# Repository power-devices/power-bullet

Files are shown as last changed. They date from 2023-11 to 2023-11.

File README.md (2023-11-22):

# Welcome to the Power Bullet electronics repository

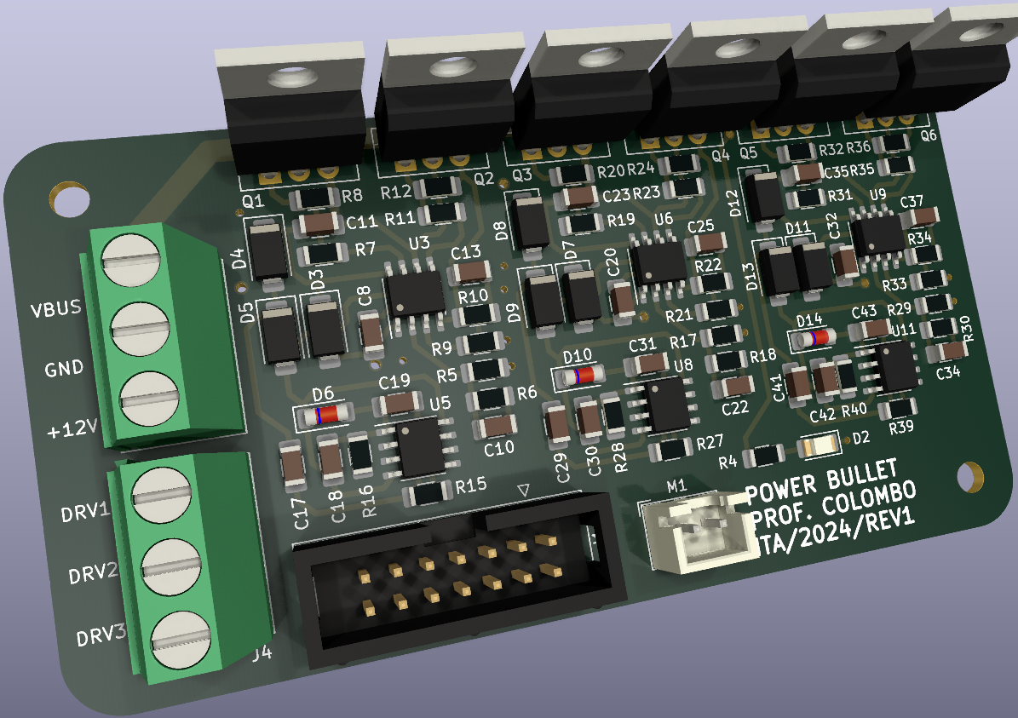
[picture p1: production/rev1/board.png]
REV1 board 3D model


I teach power electronics and I want to provide my students the best experience possible. This is the reason I created this project. I intend to allow people to produce power electronics devices at an extreme low cost. This board required 4 layers, but this is no problem today due to [JLCPCB](https://jlcpcb.com/) or other manufacturers.

So far, the project is divided into 3 pieces:

 1. Power supply: used to delivery power the other boards, it is compatible with mono-three phase up to 220 VAC
 2. Power bullet: a three phase h-bridge, simple as that
 3. Power brain F103: the main controller

# Disclaimer

I provide no warranty at all. Use it at your own risk!

# What will I find here?

You will find the design and production files. To edit the schematic/board you will need to install Kicad. I used version 7 to create this board.

# What can I do with this?

In this repository the board design and production files are stored. You are welcome to download/distribute it, use it, whatever.

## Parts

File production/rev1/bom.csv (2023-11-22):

Designator | Footprint | Quantity | Value | LCSC Part #
C1, C14, C20, C26, C32, C5, C8 | 1206 | 7 | 1uF
C10, C13, C22, C25, C34, C37 | 1206 | 6 | 33nF
C11, C23, C35 | 1206 | 3 | 1uF/50V
C15, C27 | 1206 | 2 | 1nF
C17, C29, C41 | 1206 | 3 | 10nF/50V
C18, C30, C42 | 1206 | 3 | 100nF/50V
C19, C31, C43 | 1206 | 3 | 1nF/50V
C2 | 1206 | 1 | 2n2
C4 | CP_EIA-3216-18_Kemet-A | 1 | 10uF
D10, D14, D6 | D_MiniMELF | 3 | ZMM15
D11, D3, D7 | D_SMA | 3 | 1N4007
D12, D13, D4, D5, D8, D9 | D_SMA | 6 | SS14
D2 | 1206 | 1 | LED
J1 | IDC-Header_2x07_P2.54mm_Vertical | 1 | Conn_02x07_Odd_Even
J3, J4 | TerminalBlock_Phoenix_MKDS-1,5-3_1x03_P5.00mm_Horizontal | 2 | Screw_Terminal_01x03
M1 | JST_XH_B2B-XH-A_1x02_P2.50mm_Vertical | 1 | Fan
Q1, Q2, Q3, Q4, Q5, Q6 | TO-220-3_Vertical | 6 | FDP11N50
R1 | 1206 | 1 | 120k
R10, R18, R22, R30, R34, R6 | 1206 | 6 | 3k3
R11, R17, R19, R21, R23, R29, R31, R33, R35, R5, R7, R9 | 1206 | 12 | 100R
R12, R20, R24, R32, R36, R8 | 1206 | 6 | 10k
R15, R16, R27, R28, R39, R40 | 1206 | 6 | 100k
R2 | 1206 | 1 | 1k5
R4 | 1206 | 1 | 220R
U11, U5, U8 | SOIC-8_3.9x4.9mm_P1.27mm | 3 | NE555D
U2 | SOT-223-3_TabPin2 | 1 | AMS1117-5.0
U3, U6, U9 | SOIC-8_3.9x4.9mm_P1.27mm | 3 | IR2101S
U4, U7 | SOIC-8_3.9x4.9mm_P1.27mm | 2 | ACS712xLCTR-05B

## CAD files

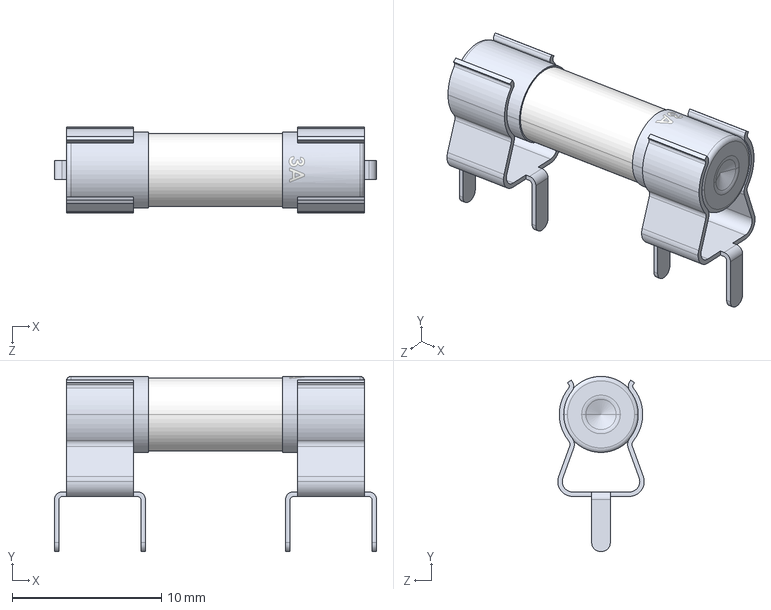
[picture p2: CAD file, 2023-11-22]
3d/Fuse Holder.STEP
21.6 x 11.8 x 5.80 mm
Fuse Clip x 2
3A Fuse

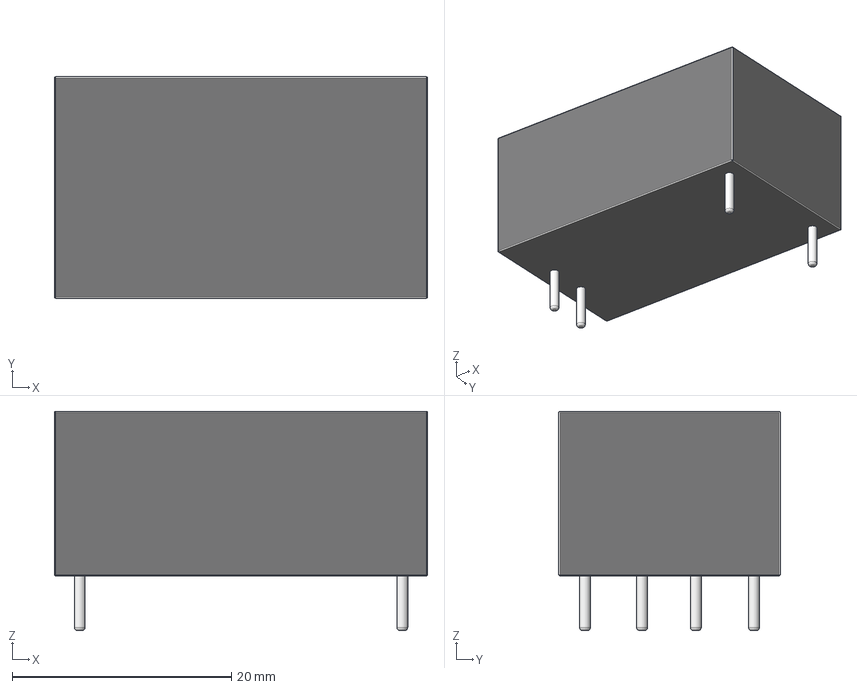
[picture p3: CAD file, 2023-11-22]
3d/hlk-pm01.step
34.0 x 20.2 x 20.0 mm

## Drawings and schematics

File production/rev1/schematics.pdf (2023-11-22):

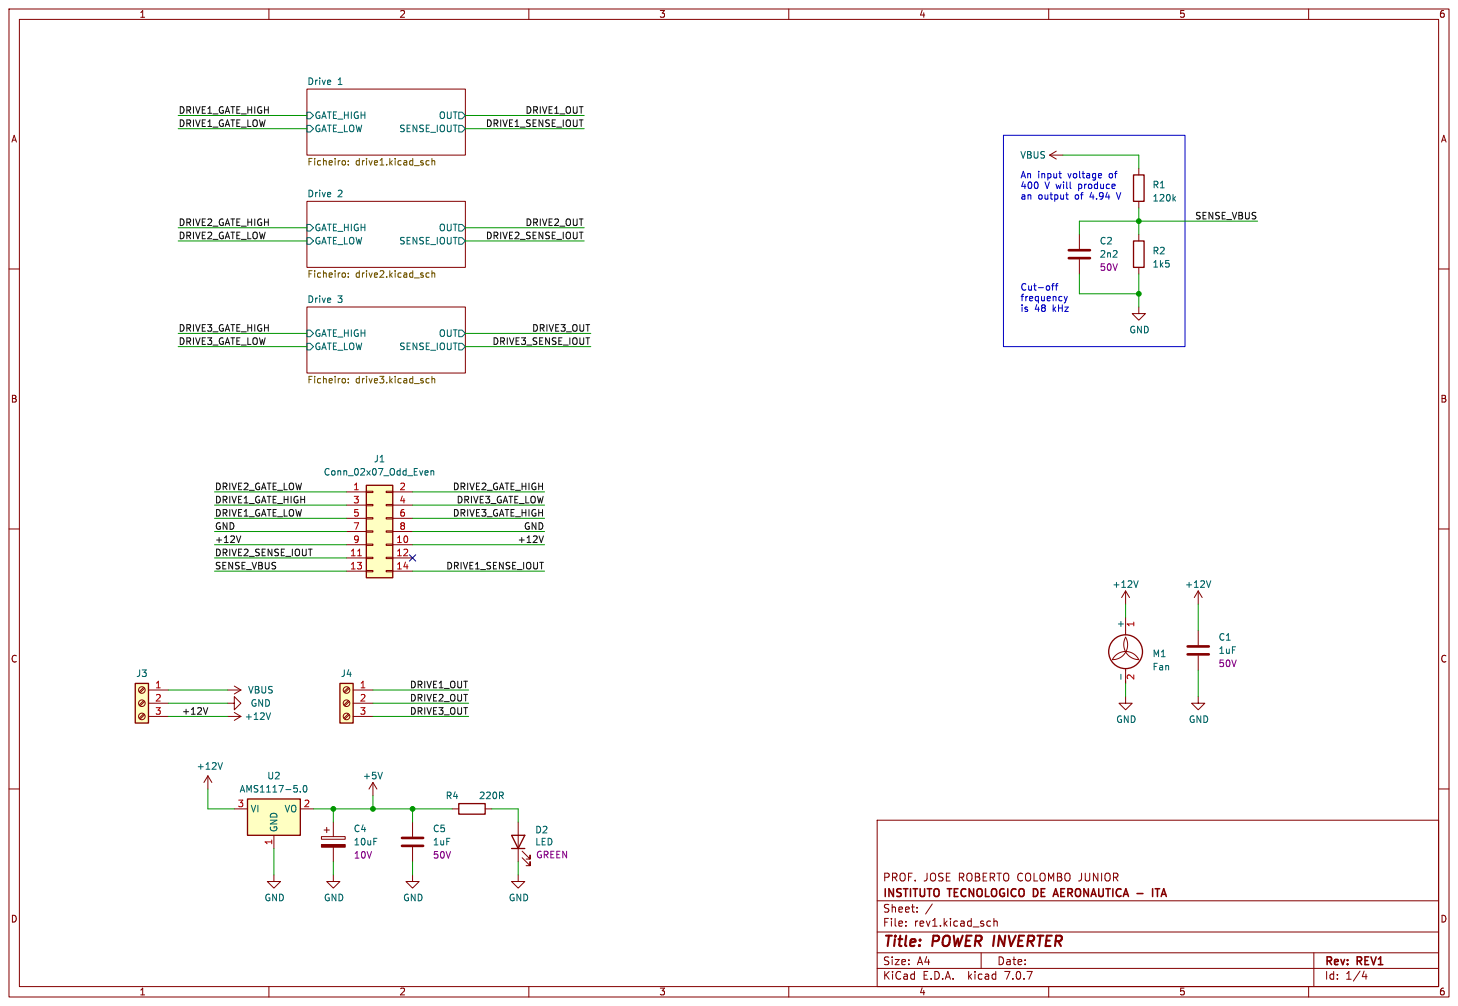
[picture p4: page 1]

is 48 kHz An input voltage of 400 V will produce

File: rev1.kicad_sch Sheet: /
Id: 1/4 Title: POWER INVERTER

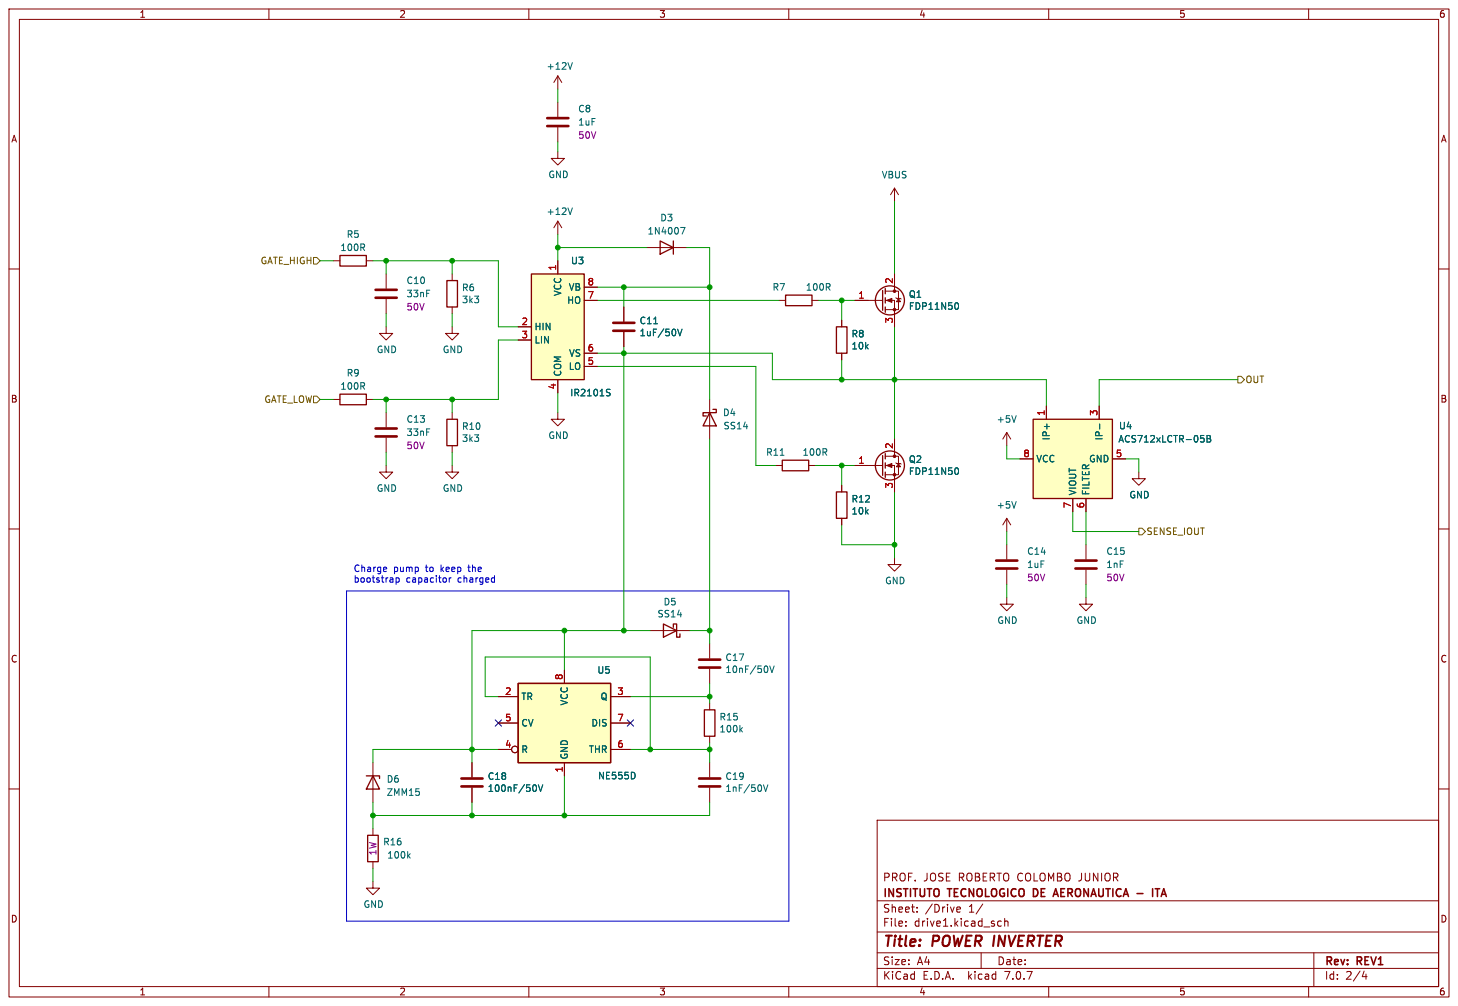
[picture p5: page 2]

OUT Charge pump to keep the

Id: 2/4 Title: POWER INVERTER

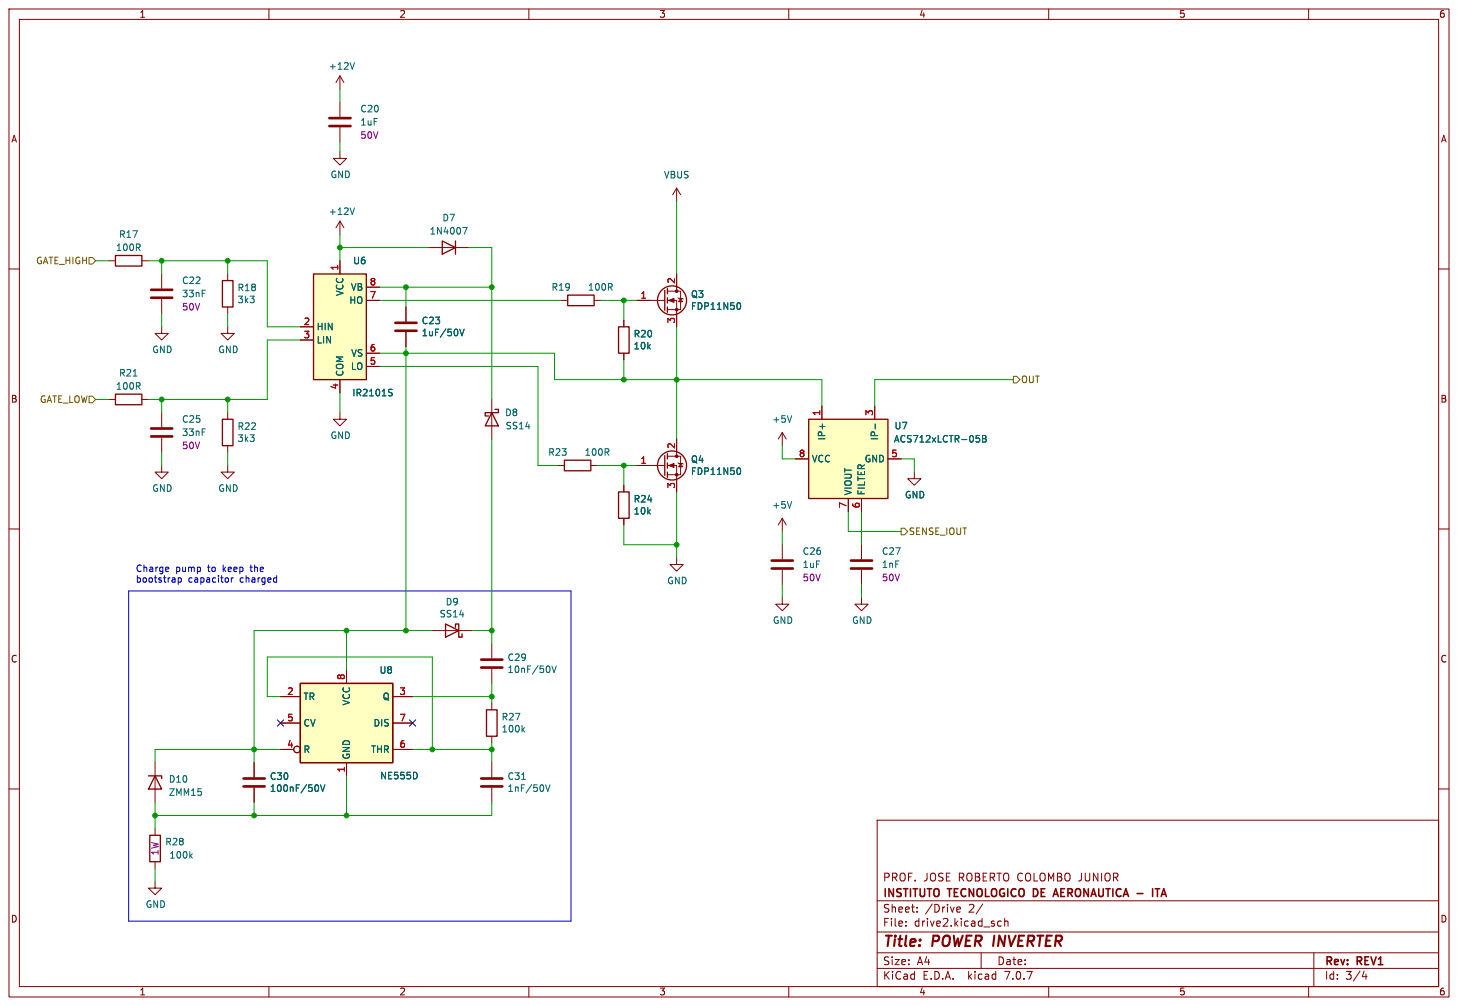
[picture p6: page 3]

Charge pump to keep the

Id: 3/4 Title: POWER INVERTER

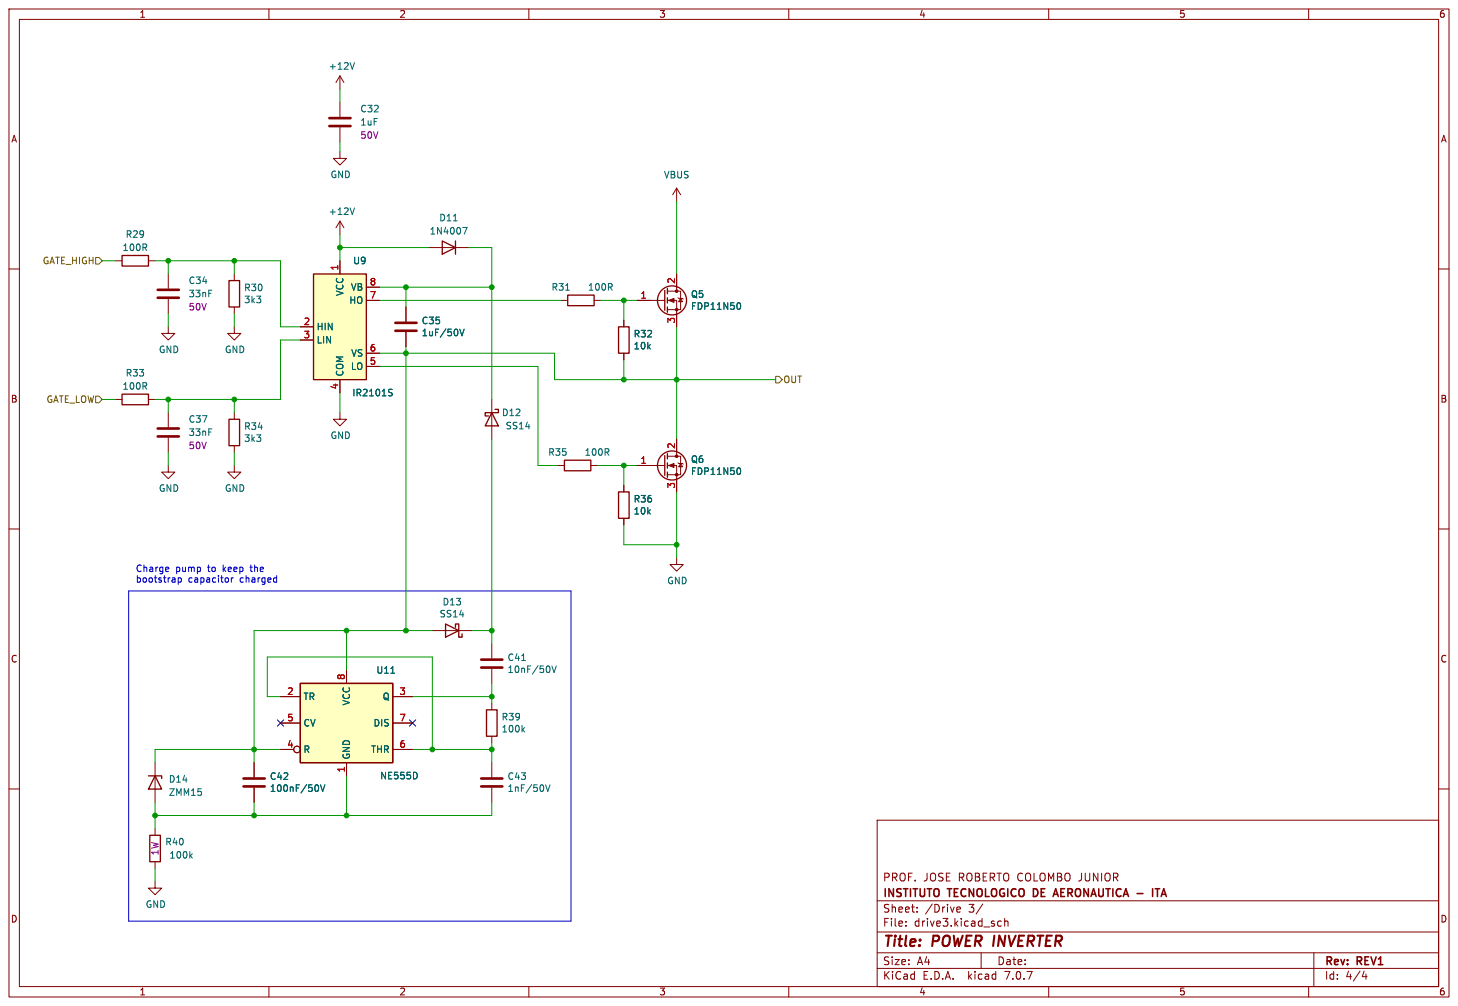
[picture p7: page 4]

Charge pump to keep the

Id: 4/4 Title: POWER INVERTER

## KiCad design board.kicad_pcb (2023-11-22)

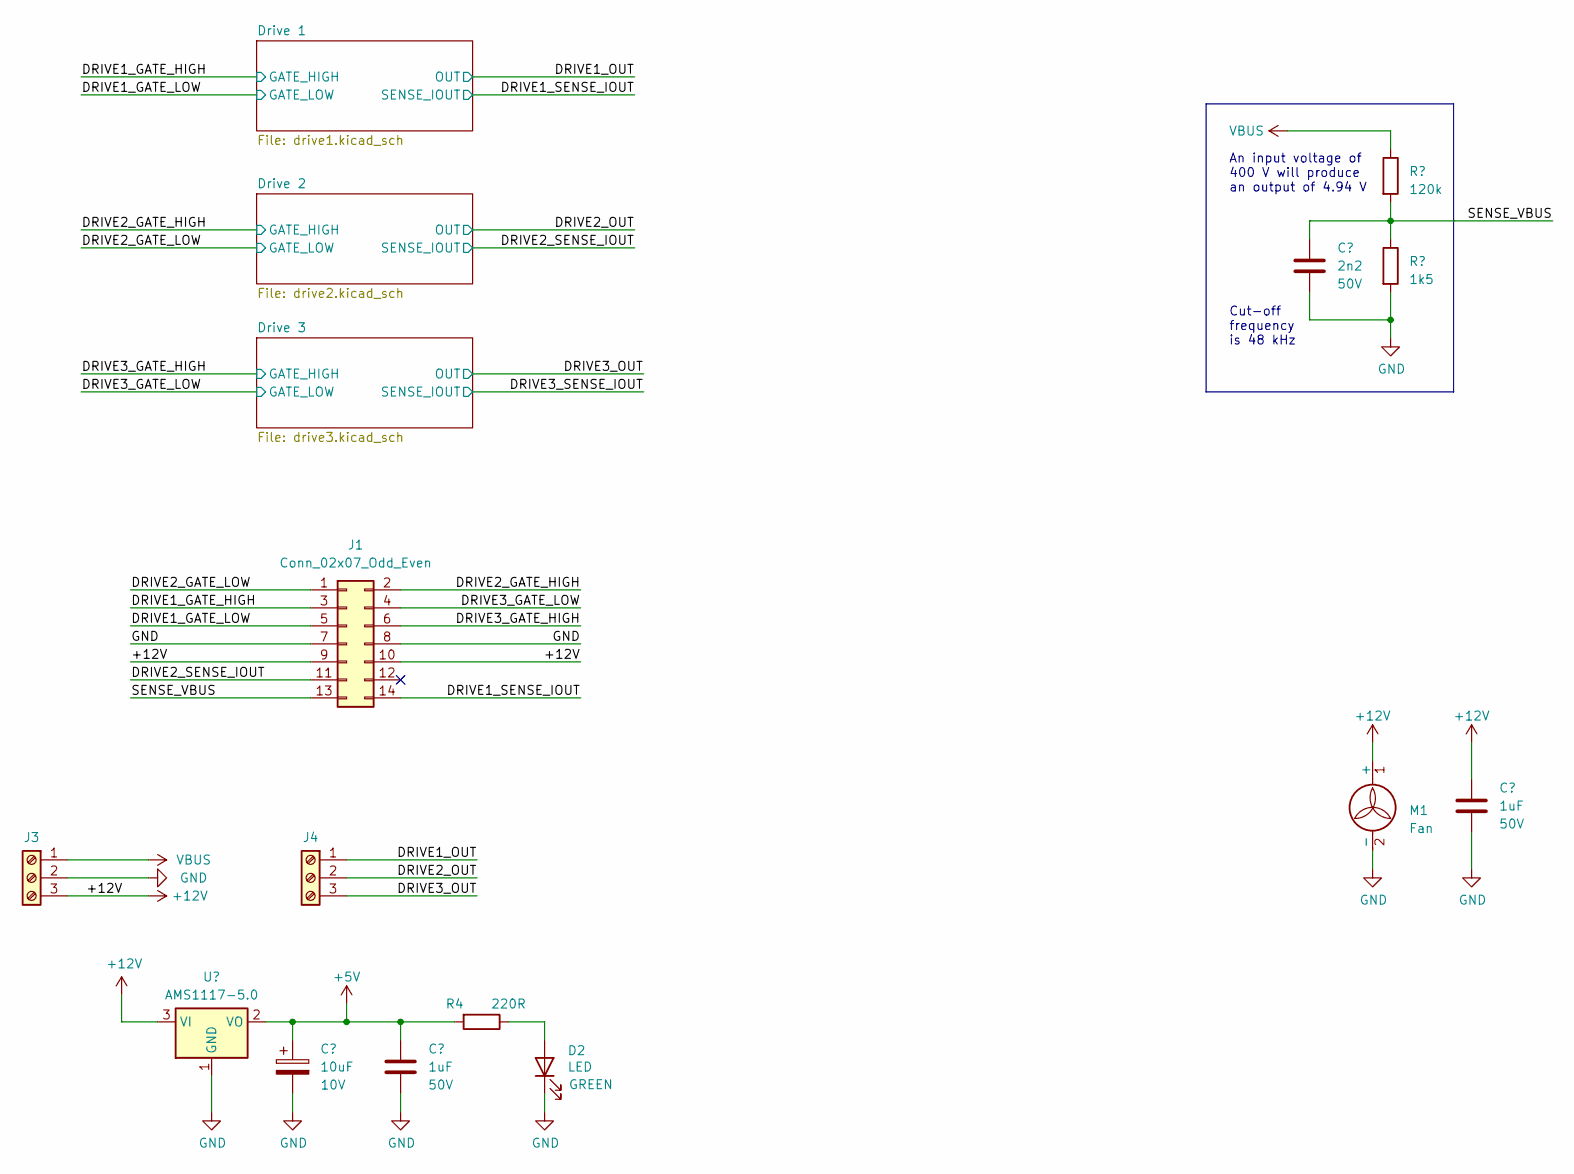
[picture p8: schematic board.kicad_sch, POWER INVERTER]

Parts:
C1, C5: 1uF; C_1206_3216Metric_Pad1.33x1.80mm_HandSolder; Voltage 50V
C2: 2n2; C_1206_3216Metric; Voltage 50V
C4: 10uF; CP_EIA-3216-18_Kemet-A; Voltage 10V
D2: LED; LED_1206_3216Metric_Pad1.42x1.75mm_HandSolder
J1: Conn_02x07_Odd_Even; IDC-Header_2x07_P2.54mm_Vertical
J3, J4: Screw_Terminal_01x03; TerminalBlock_Phoenix_MKDS-1,5-3_1x03_P5.00mm_Horizontal
M1: Fan; JST_XH_B2B-XH-A_1x02_P2.50mm_Vertical
R1: 120k; R_1206_3216Metric_Pad1.30x1.75mm_HandSolder
R2: 1k5; R_1206_3216Metric_Pad1.30x1.75mm_HandSolder
R4: 220R; R_1206_3216Metric_Pad1.30x1.75mm_HandSolder
U2: AMS1117-5.0; SOT-223-3_TabPin2

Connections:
+5V: C4.1, C5.1, R4.2, U2.2 (VO); also elsewhere on the board
+12V: C1.1, J1.9, J1.10, J3.3, M1.1 (+), U2.3 (VI); also elsewhere on the board
/DRIVE1_GATE_HIGH: J1.3; also elsewhere on the board
/DRIVE1_GATE_LOW: J1.5; also elsewhere on the board
/DRIVE1_OUT: J4.1; also elsewhere on the board
/DRIVE1_SENSE_IOUT: J1.14; also elsewhere on the board
/DRIVE2_GATE_HIGH: J1.2; also elsewhere on the board
/DRIVE2_GATE_LOW: J1.1; also elsewhere on the board
/DRIVE2_OUT: J4.2; also elsewhere on the board
/DRIVE2_SENSE_IOUT: J1.11; also elsewhere on the board
/DRIVE3_GATE_HIGH: J1.6; also elsewhere on the board
/DRIVE3_GATE_LOW: J1.4; also elsewhere on the board
/DRIVE3_OUT: J4.3; also elsewhere on the board
/SENSE_VBUS: C2.1, J1.13, R1.2, R2.1
GND: C1.2, C2.2, C4.2, C5.2, D2.1 (K), J1.7, J1.8, J3.2, M1.2 (-), R2.2, U2.1 (GND); also elsewhere on the board
unnamed: D2.2 (A), R4.1
VBUS: J3.1, R1.1; also elsewhere on the board

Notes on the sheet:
An input voltage of 400 V will produce an output of 4.94 V
Cut-off frequency is 48 kHz

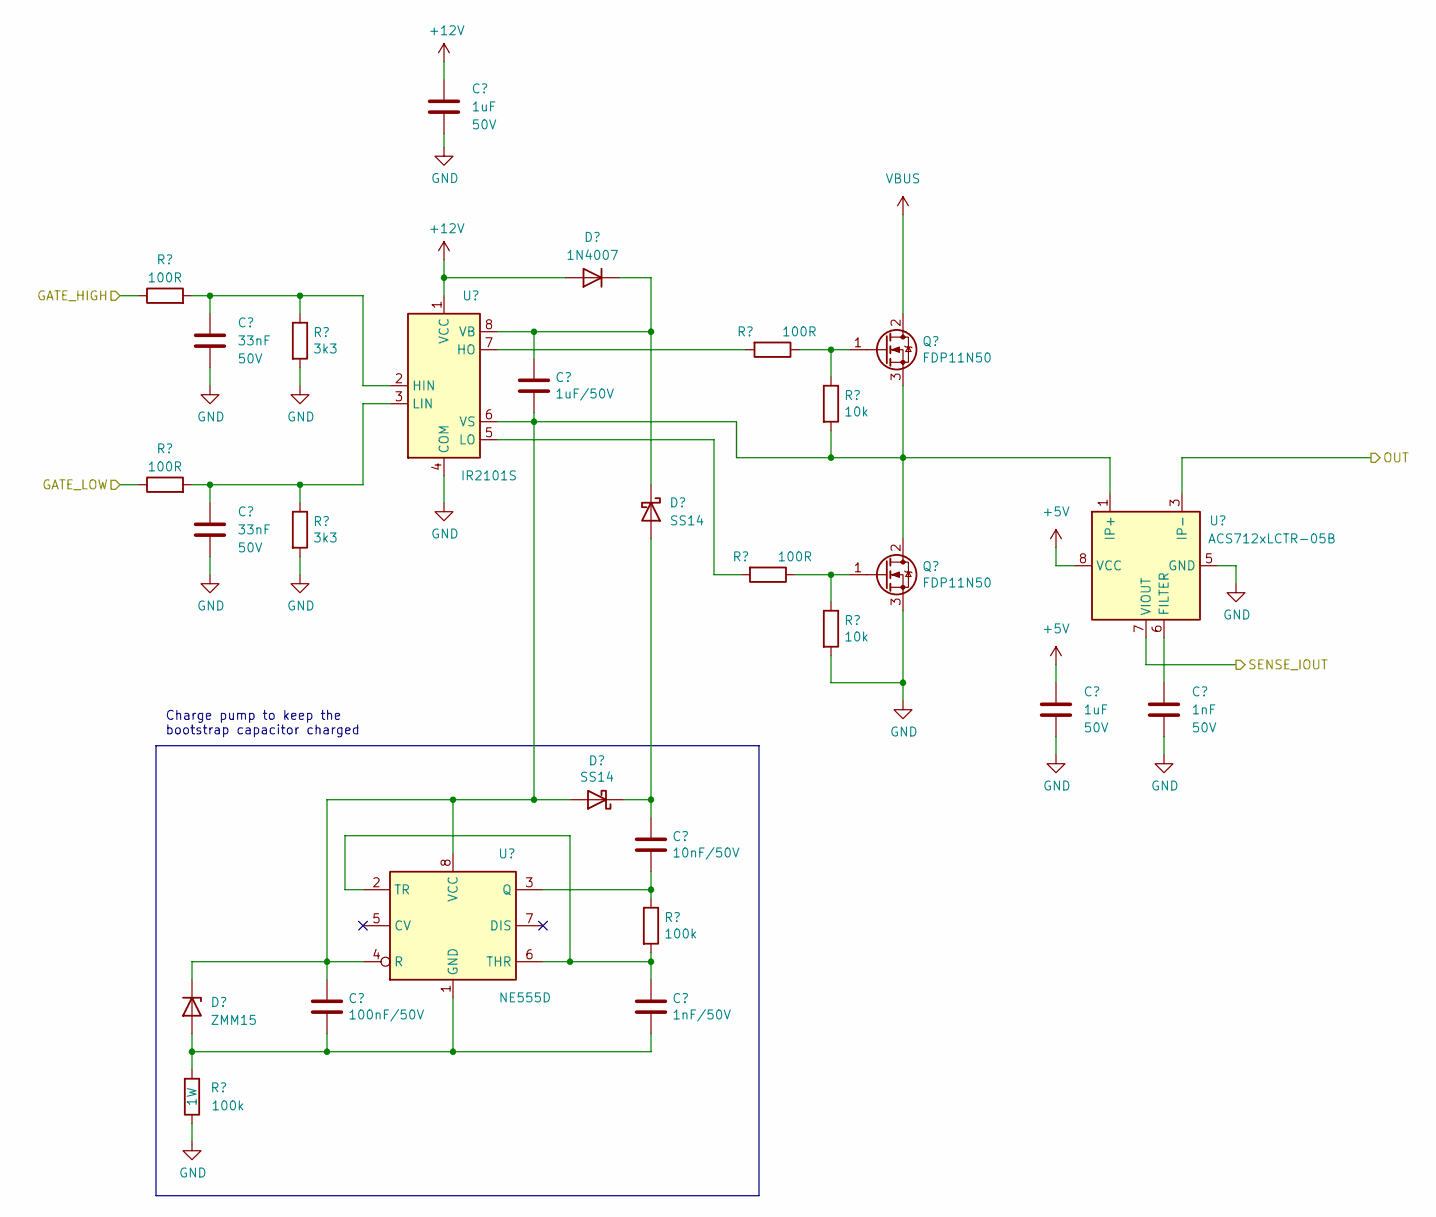
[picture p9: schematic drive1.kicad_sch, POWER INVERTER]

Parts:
C8, C14: 1uF; C_1206_3216Metric_Pad1.33x1.80mm_HandSolder; Voltage 50V
C10, C13: 33nF; C_1206_3216Metric; Voltage 50V
C11: 1uF/50V; C_1206_3216Metric_Pad1.33x1.80mm_HandSolder
C15: 1nF; C_1206_3216Metric_Pad1.33x1.80mm_HandSolder; Voltage 50V
C17: 10nF/50V; C_1206_3216Metric_Pad1.33x1.80mm_HandSolder
C18: 100nF/50V; C_1206_3216Metric_Pad1.33x1.80mm_HandSolder
C19: 1nF/50V; C_1206_3216Metric_Pad1.33x1.80mm_HandSolder
D3: 1N4007; D_SMA
D4, D5: SS14; D_SMA
D6: ZMM15; D_MiniMELF
Q1, Q2: FDP11N50; TO-220-3_Vertical
R5, R7, R9, R11: 100R; R_1206_3216Metric_Pad1.30x1.75mm_HandSolder
R6, R10: 3k3; R_1206_3216Metric_Pad1.30x1.75mm_HandSolder
R8, R12: 10k; R_1206_3216Metric_Pad1.30x1.75mm_HandSolder
R15: 100k; R_1206_3216Metric_Pad1.30x1.75mm_HandSolder
R16: 100k; R_1206_3216Metric
U3: IR2101S; SOIC-8_3.9x4.9mm_P1.27mm
U4: ACS712xLCTR-05B; SOIC-8_3.9x4.9mm_P1.27mm
U5: NE555D; SOIC-8_3.9x4.9mm_P1.27mm

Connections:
+5V: C14.1, U4.8 (VCC); also elsewhere on the board
+12V: C8.1, D3.2 (A), U3.1 (VCC); also elsewhere on the board
/DRIVE1_GATE_HIGH: R5.1; also elsewhere on the board
/DRIVE1_GATE_LOW: R9.1; also elsewhere on the board
/DRIVE1_OUT: U4.3 (IP-), U4.4 (IP-); also elsewhere on the board
/DRIVE1_SENSE_IOUT: U4.7 (VIOUT); also elsewhere on the board
GND: C8.2, C10.2, C13.2, C14.2, C15.2, Q2.3 (S), R6.2, R10.2, R12.2, R16.1, U3.4 (COM), U4.5 (GND); also elsewhere on the board
unnamed: C11.1, D3.1 (K), D4.1 (K), U3.8 (VB)
unnamed: C17.1, D4.2 (A), D5.1 (K)
unnamed: C11.2, C18.1, D5.2 (A), D6.1 (K), Q1.3 (S), Q2.2 (D), R8.2, U3.6 (VS), U4.1 (IP+), U4.2 (IP+), U5.4 (R), U5.8 (VCC)
unnamed: C18.2, C19.2, D6.2 (A), R16.2, U5.1 (GND)
unnamed: Q1.1 (G), R7.1, R8.1
unnamed: Q2.1 (G), R11.1, R12.1
unnamed: C10.1, R5.2, R6.1, U3.2 (HIN)
unnamed: R7.2, U3.7 (HO)
unnamed: C13.1, R9.2, R10.1, U3.3 (LIN)
unnamed: R11.2, U3.5 (LO)
unnamed: C15.1, U4.6 (FILTER)
unnamed: C17.2, R15.1, U5.3 (Q)
unnamed: C19.1, R15.2, U5.2 (TR), U5.6 (THR)
VBUS: Q1.2 (D); also elsewhere on the board

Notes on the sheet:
Charge pump to keep the bootstrap capacitor charged

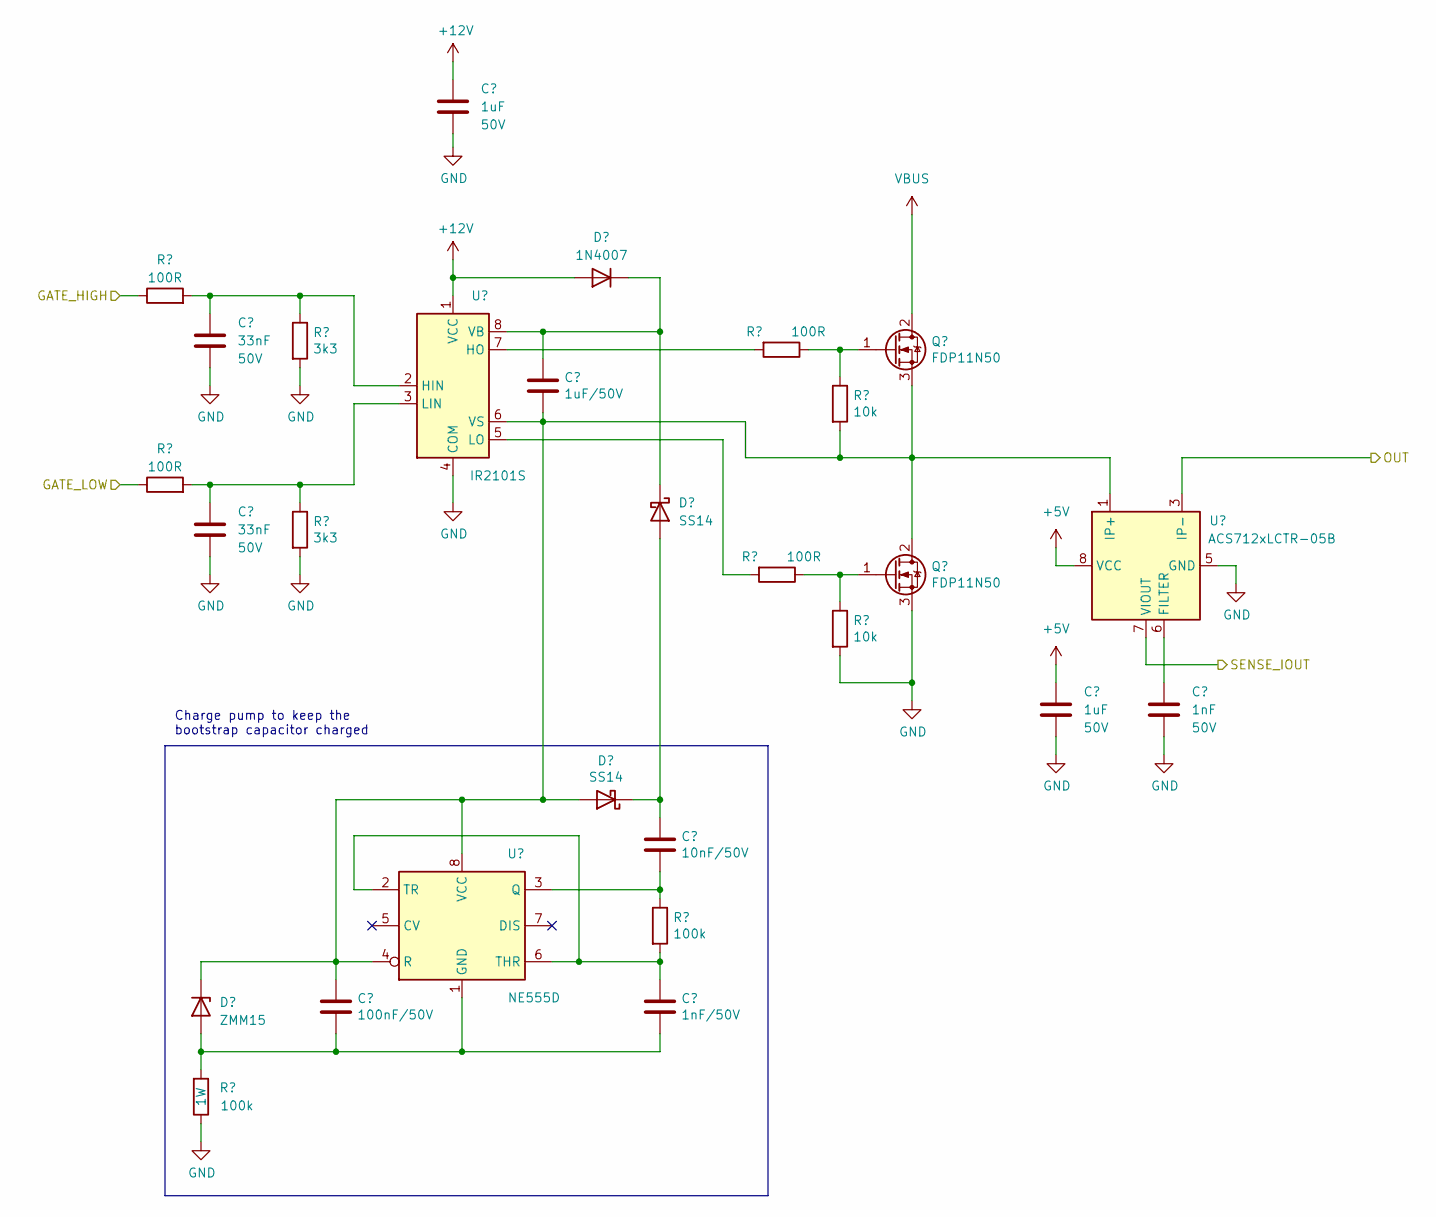
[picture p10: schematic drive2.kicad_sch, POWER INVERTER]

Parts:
C20, C26: 1uF; C_1206_3216Metric_Pad1.33x1.80mm_HandSolder; Voltage 50V
C22, C25: 33nF; C_1206_3216Metric; Voltage 50V
C23: 1uF/50V; C_1206_3216Metric_Pad1.33x1.80mm_HandSolder
C27: 1nF; C_1206_3216Metric_Pad1.33x1.80mm_HandSolder; Voltage 50V
C29: 10nF/50V; C_1206_3216Metric_Pad1.33x1.80mm_HandSolder
C30: 100nF/50V; C_1206_3216Metric_Pad1.33x1.80mm_HandSolder
C31: 1nF/50V; C_1206_3216Metric_Pad1.33x1.80mm_HandSolder
D7: 1N4007; D_SMA
D8, D9: SS14; D_SMA
D10: ZMM15; D_MiniMELF
Q3, Q4: FDP11N50; TO-220-3_Vertical
R17, R19, R21, R23: 100R; R_1206_3216Metric_Pad1.30x1.75mm_HandSolder
R18, R22: 3k3; R_1206_3216Metric_Pad1.30x1.75mm_HandSolder
R20, R24: 10k; R_1206_3216Metric_Pad1.30x1.75mm_HandSolder
R27, R28: 100k; R_1206_3216Metric_Pad1.30x1.75mm_HandSolder
U6: IR2101S; SOIC-8_3.9x4.9mm_P1.27mm
U7: ACS712xLCTR-05B; SOIC-8_3.9x4.9mm_P1.27mm
U8: NE555D; SOIC-8_3.9x4.9mm_P1.27mm

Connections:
+5V: C26.1, U7.8 (VCC); also elsewhere on the board
+12V: C20.1, D7.2 (A), U6.1 (VCC); also elsewhere on the board
/DRIVE2_GATE_HIGH: R17.1; also elsewhere on the board
/DRIVE2_GATE_LOW: R21.1; also elsewhere on the board
/DRIVE2_OUT: U7.3 (IP-), U7.4 (IP-); also elsewhere on the board
/DRIVE2_SENSE_IOUT: U7.7 (VIOUT); also elsewhere on the board
GND: C20.2, C22.2, C25.2, C26.2, C27.2, Q4.3 (S), R18.2, R22.2, R24.2, R28.1, U6.4 (COM), U7.5 (GND); also elsewhere on the board
unnamed: C23.1, D7.1 (K), D8.1 (K), U6.8 (VB)
unnamed: C29.1, D8.2 (A), D9.1 (K)
unnamed: C30.2, C31.2, D10.2 (A), R28.2, U8.1 (GND)
unnamed: C23.2, C30.1, D9.2 (A), D10.1 (K), Q3.3 (S), Q4.2 (D), R20.2, U6.6 (VS), U7.1 (IP+), U7.2 (IP+), U8.4 (R), U8.8 (VCC)
unnamed: Q3.1 (G), R19.1, R20.1
unnamed: Q4.1 (G), R23.1, R24.1
unnamed: C22.1, R17.2, R18.1, U6.2 (HIN)
unnamed: R19.2, U6.7 (HO)
unnamed: C25.1, R21.2, R22.1, U6.3 (LIN)
unnamed: R23.2, U6.5 (LO)
unnamed: C27.1, U7.6 (FILTER)
unnamed: C29.2, R27.1, U8.3 (Q)
unnamed: C31.1, R27.2, U8.2 (TR), U8.6 (THR)
VBUS: Q3.2 (D); also elsewhere on the board

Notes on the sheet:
Charge pump to keep the bootstrap capacitor charged

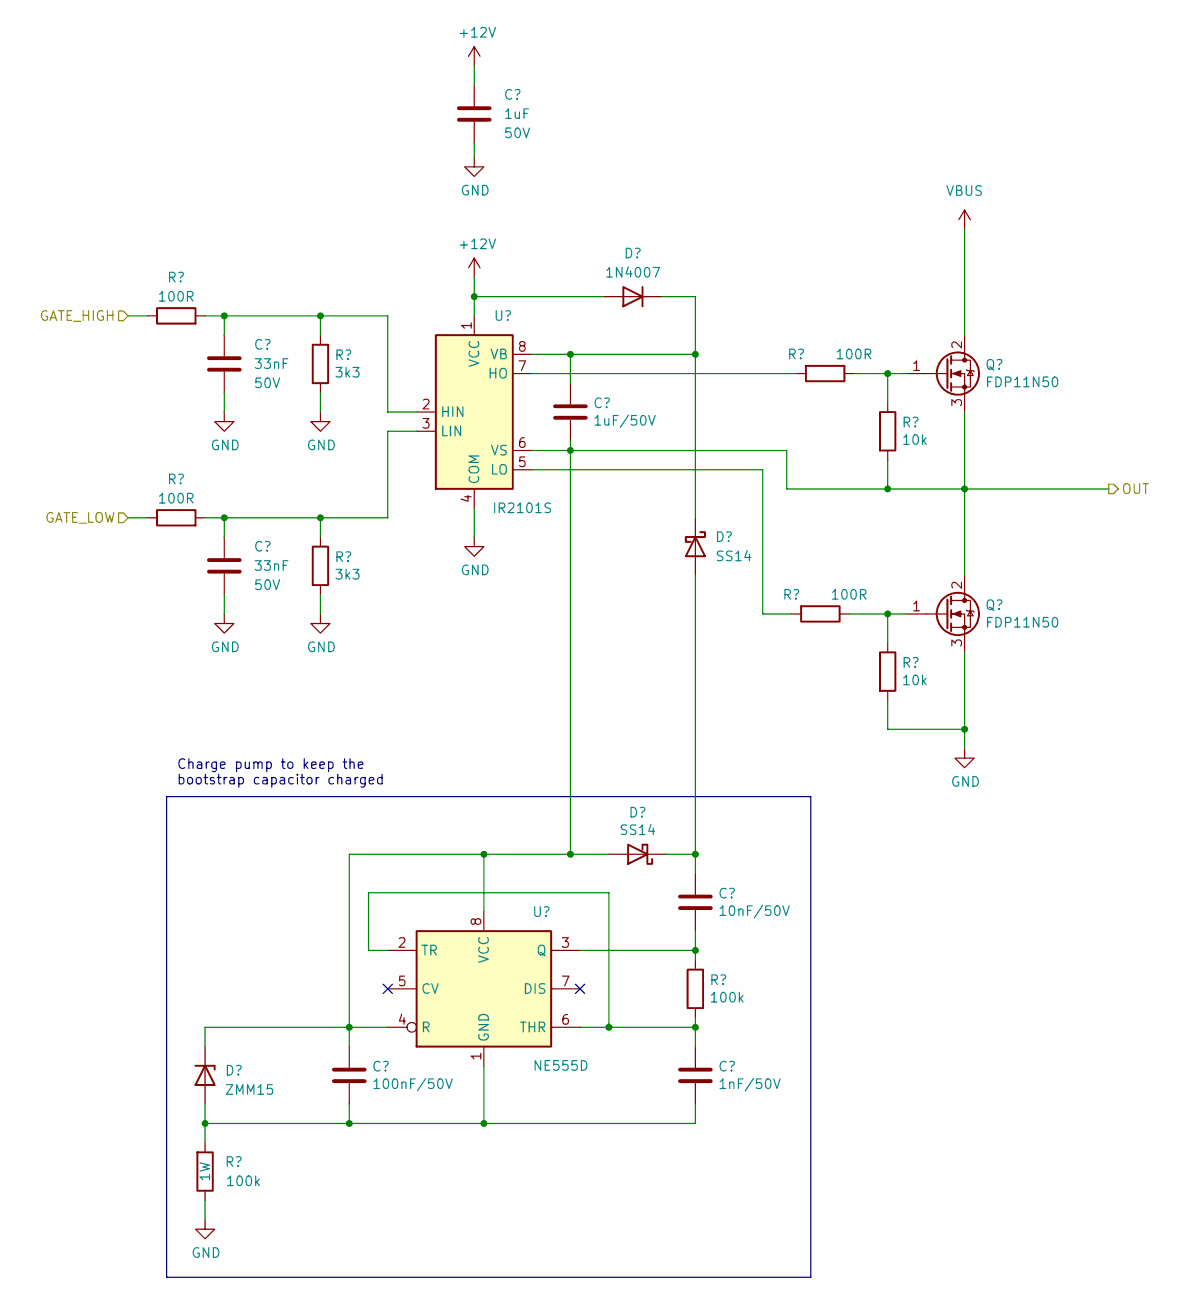
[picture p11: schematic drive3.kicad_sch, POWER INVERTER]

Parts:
C32: 1uF; C_1206_3216Metric_Pad1.33x1.80mm_HandSolder; Voltage 50V
C34, C37: 33nF; C_1206_3216Metric; Voltage 50V
C35: 1uF/50V; C_1206_3216Metric_Pad1.33x1.80mm_HandSolder
C41: 10nF/50V; C_1206_3216Metric_Pad1.33x1.80mm_HandSolder
C42: 100nF/50V; C_1206_3216Metric_Pad1.33x1.80mm_HandSolder
C43: 1nF/50V; C_1206_3216Metric_Pad1.33x1.80mm_HandSolder
D11: 1N4007; D_SMA
D12, D13: SS14; D_SMA
D14: ZMM15; D_MiniMELF
Q5, Q6: FDP11N50; TO-220-3_Vertical
R29, R31, R33, R35: 100R; R_1206_3216Metric_Pad1.30x1.75mm_HandSolder
R30, R34: 3k3; R_1206_3216Metric_Pad1.30x1.75mm_HandSolder
R32, R36: 10k; R_1206_3216Metric_Pad1.30x1.75mm_HandSolder
R39, R40: 100k; R_1206_3216Metric_Pad1.30x1.75mm_HandSolder
U9: IR2101S; SOIC-8_3.9x4.9mm_P1.27mm
U11: NE555D; SOIC-8_3.9x4.9mm_P1.27mm

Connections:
+12V: C32.1, D11.2 (A), U9.1 (VCC); also elsewhere on the board
/DRIVE3_GATE_HIGH: R29.1; also elsewhere on the board
/DRIVE3_GATE_LOW: R33.1; also elsewhere on the board
/DRIVE3_OUT: C35.2, C42.1, D13.2 (A), D14.1 (K), Q5.3 (S), Q6.2 (D), R32.2, U9.6 (VS), U11.4 (R), U11.8 (VCC); also elsewhere on the board
GND: C32.2, C34.2, C37.2, Q6.3 (S), R30.2, R34.2, R36.2, R40.1, U9.4 (COM); also elsewhere on the board
unnamed: C35.1, D11.1 (K), D12.1 (K), U9.8 (VB)
unnamed: C41.1, D12.2 (A), D13.1 (K)
unnamed: C42.2, C43.2, D14.2 (A), R40.2, U11.1 (GND)
unnamed: Q5.1 (G), R31.1, R32.1
unnamed: Q6.1 (G), R35.1, R36.1
unnamed: C34.1, R29.2, R30.1, U9.2 (HIN)
unnamed: R31.2, U9.7 (HO)
unnamed: C37.1, R33.2, R34.1, U9.3 (LIN)
unnamed: R35.2, U9.5 (LO)
unnamed: C41.2, R39.1, U11.3 (Q)
unnamed: C43.1, R39.2, U11.2 (TR), U11.6 (THR)
VBUS: Q5.2 (D); also elsewhere on the board

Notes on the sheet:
Charge pump to keep the bootstrap capacitor charged

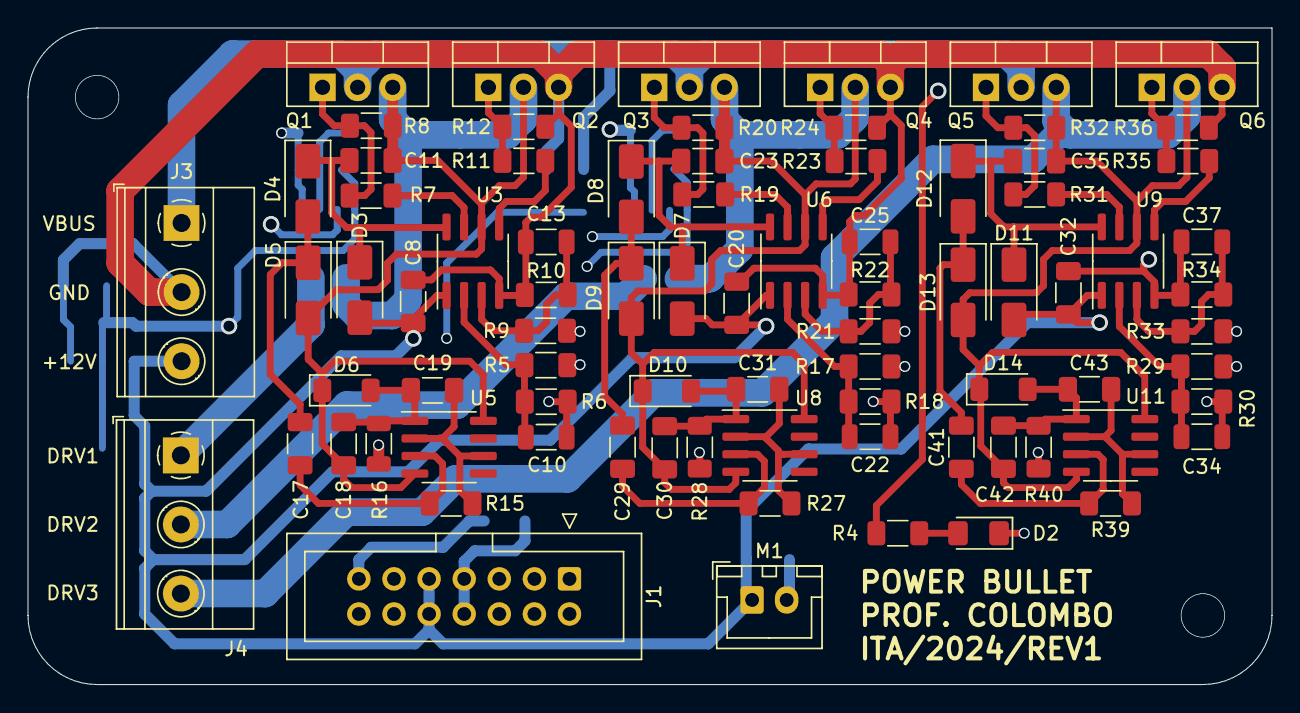
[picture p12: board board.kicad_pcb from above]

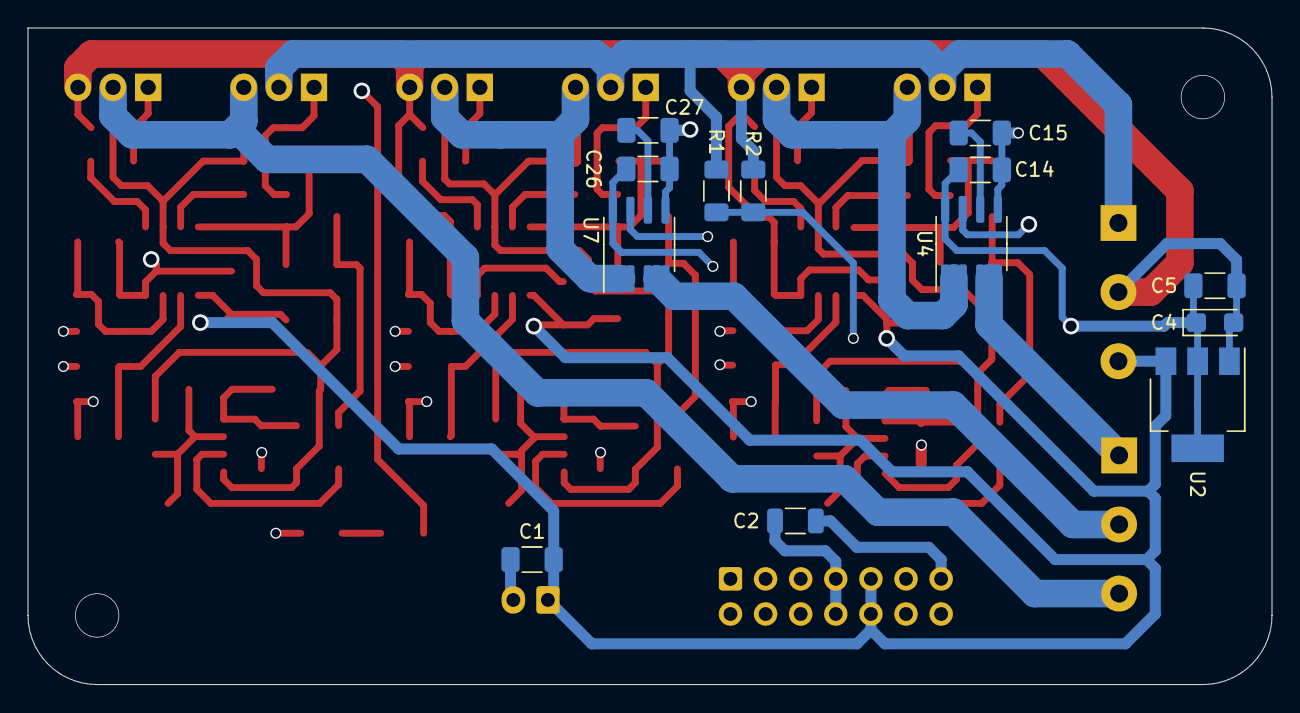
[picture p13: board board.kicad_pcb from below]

Board: 4 copper layers, 90.0 x 47.5 mm, 94 parts (13 on the bottom side), 54 nets.
